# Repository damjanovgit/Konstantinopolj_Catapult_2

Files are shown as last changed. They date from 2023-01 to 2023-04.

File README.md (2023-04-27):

# Konstantinopolj_Catapult_2
Микроконтролерски системи/Рачунарска електроника, зимски семестар, ак. 2022/2023. година
<br />
<br />
<p align="center">


# Упутство за повезивање катапулта

## Напајање плочице
<p align="justify">Како је задано и пројектним задатком, напајање које се доводи на плочицу износи 12 V. Напајање се у овом случају доводи са протоборда (кориштењем мултиметра претходно је  увијек неопходно провјерити да ли напајање доиста одговара 12 V), а на слици су приказана и минимална повезивања. Краткоспојник жуте боје одговара 12 V, док је плавим означено уземљење, као што се да примијетити на слици. 
<br />
<br />
<p align="center">


## Повезивање плочице са програматором 
<p align="justify">За програмирање микроконтролера користи се програматор PICkit верзије 3. Наредна слика показује pinout који користи овај програматор, при чему стрелица ка доле означава пин MCLR, односно, како је приказано ознакама на слици слијева:
<br />
<br />
<p align="center">


<p align="justify">На слици здесна приказано је повезивање програматора са плочицом. Пет конектора на које треба повезати пинове програматора налази се унутар црвеног блока, те редослијед који је претходно поменут важи уколико вршимо повезивање као на слици.

## Повезивање корачних мотора са плочицом

<p align="justify">За рад са катапултом кориштено је шест корачних мотора. Од тог броја два корачна мотора користе се за кретање ласера, преостала четири су на самом катапулту,означени са О (окретање), N (натезање), К (кашика) те P (пуцање). Мотор са ознаком О омогућава окретање самог катапулта, а претходно поменути мотори са ознакама N, K и  P приказани су  на слици испод. 
<br />
<br />


Слиједи и повезивање корачних мотора са плочицом. На слици је приказан распоред повезивања, гдје се неозначени корачни мотори односе на ласере. 
<br />
<br />
<p align="center">


## Повезивање са рачунаром

<p align="justify">За везу са рачунаром  користи се USB-UART модул. Са претходно инсталираном верзијом одговарајућег драјвера за FT232RL неопходно је повезати рачунар и модул који се налази на плочици. 

<br />
<br />
<p align="center">


## Програмирање и управљање катапултом
<p align="justify">Преостаје  упалити напајање, а затим на плочици омогућити програмирање микроконтролера. Наредна слика приказује које краткоспојнике треба повезати приликом програмирања (смеђи и зелени), а затим и након што се микроконтролер успјешно испрограмира (црни и зелени). 
<br />
<br />
<p align="center">


<p align="justify">Пројекат у MikroC-у (фолдер Software/PIC24) компајлирати, а затим изгенерисан .hex унијети у MPLAB IDE софтвер за програмирање. Ући у апликацију (софтвер Processing) и учитати пројекат (фолдер Software/Processing), да би  се затим управљало катапултом, са контролним командама наведеним у табели испод.
<br />
<br />

|  Команда | Функционалност 
|---|---
|  А или а | помјерање првог ласера улијево  
|  D или d | помјерање првог ласера удесно
|  J или j | помјерање другог ласера улијево 
|  L или l | помјерање другог ласера удесно
|  C или c | калибрација
|  S или s | синхронизација ласера са апликациjом
|  space | гађање мете

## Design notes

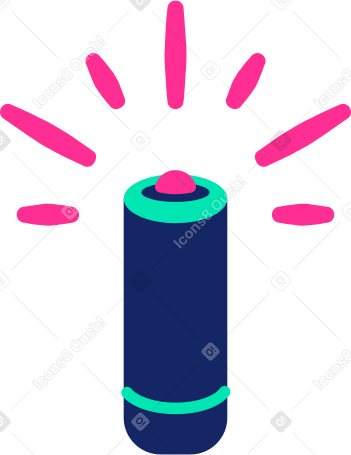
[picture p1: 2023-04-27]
Software/Processing/laser.png

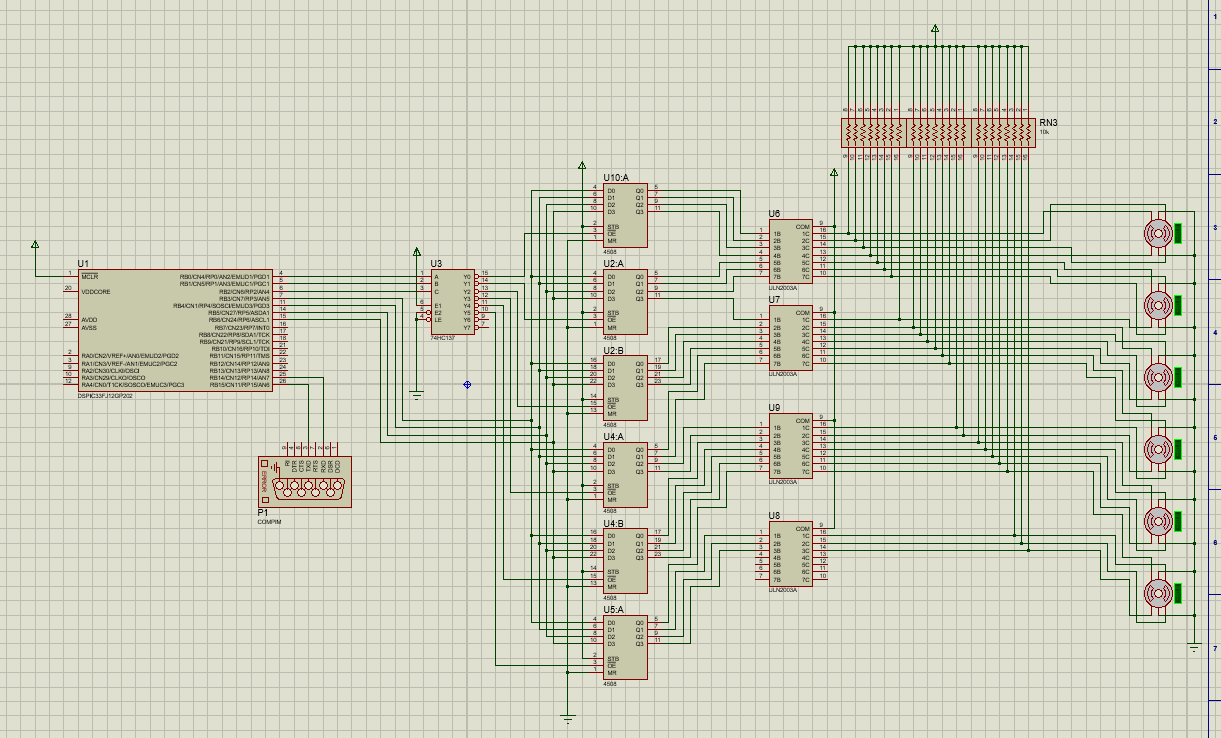
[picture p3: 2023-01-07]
Proteus simulacija/Sema.png

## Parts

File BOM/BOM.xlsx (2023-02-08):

Date: | 31-1-2023
Tool: | Eeschema (6.0.2)
Component Count: | 95
Individual Components:
Item | Qty | Reference(s) | Value | Footprint
 |  | C0 | 0.1uF | footprints:08055A220JAT2A
 |  | C1 | 0.1uF | footprints:08055A220JAT2A
 |  | C2 | 100uF | footprints:08055A220JAT2A
 |  | C3 | 22pF | footprints:08055A220JAT2A
 |  | C4 | 22pF | footprints:08055A220JAT2A
 |  | C5 | 0.1uF | footprints:08055A220JAT2A
 |  | C6 | 0.1uF | footprints:08055A220JAT2A
 |  | C7 | 100uF | footprints:08055A220JAT2A
 |  | C8 | 0.1uF | footprints:08055A220JAT2A
 |  | C9 | 0.1uF | footprints:08055A220JAT2A
 |  | C10 | 0.1uF | footprints:08055A220JAT2A
 |  | C11 | 0.1uF | footprints:08055A220JAT2A
 |  | C12 | 10uF | footprints:08055A220JAT2A
 |  | C13 | 0.1uF | footprints:08055A220JAT2A
 |  | C14 | 0.1uF | footprints:08055A220JAT2A
 |  | C15 | 0.1uF | footprints:08055A220JAT2A
 |  | C16 | 0.1uF | footprints:08055A220JAT2A
 |  | C17 | 0.1uF | footprints:08055A220JAT2A
 |  | C18 | 0.1uF | footprints:08055A220JAT2A
 |  | C19 | 0.1uF | footprints:08055A220JAT2A
 |  | C20 | 0.1uF | footprints:08055A220JAT2A
 |  | C21 | 0.1uF | footprints:08055A220JAT2A
 |  | C22 | 0.1uF | footprints:08055A220JAT2A
 |  | H1 | MountingHole | MountingHole:MountingHole_3.5mm | ~
 |  | H2 | MountingHole | MountingHole:MountingHole_3.5mm | ~
 |  | H3 | MountingHole | MountingHole:MountingHole_3.5mm | ~
 |  | H4 | MountingHole | MountingHole:MountingHole_3.5mm | ~
 |  | J1 | Conn_01x05_Male | Connector_PinHeader_1.00mm:PinHeader_1x05_P1.00mm_Vertical | ~
 |  | J2 | Conn_01x01_Male | Connector_PinHeader_1.00mm:PinHeader_1x01_P1.00mm_Vertical | ~
 |  | J3 | Conn_01x03_Male | Connector_PinHeader_1.00mm:PinHeader_1x03_P1.00mm_Vertical | ~
 |  | J4 | Conn_01x05_Male | Connector_PinHeader_1.00mm:PinHeader_1x05_P1.00mm_Vertical | ~
 |  | J5 | Conn_01x03_Male | Connector_PinHeader_1.00mm:PinHeader_1x03_P1.00mm_Vertical | ~
 |  | J6 | USB_B | Connector_USB:USB_B_TE_5787834_Vertical | ~
 |  | J7 | Conn_01x05_Male | Connector_PinHeader_1.00mm:PinHeader_1x05_P1.00mm_Vertical | ~
 |  | J8 | Conn_01x05_Male | Connector_PinHeader_1.00mm:PinHeader_1x05_P1.00mm_Vertical | ~
 |  | J9 | Conn_01x05_Male | Connector_PinHeader_1.00mm:PinHeader_1x05_P1.00mm_Vertical | ~
 |  | J10 | Conn_01x05_Male | Connector_PinHeader_1.00mm:PinHeader_1x05_P1.00mm_Vertical | ~
 |  | J11 | Conn_01x05_Male | Connector_PinHeader_1.00mm:PinHeader_1x05_P1.00mm_Vertical | ~
 |  | J12 | Conn_01x05_Male | Connector_PinHeader_1.00mm:PinHeader_1x05_P1.00mm_Vertical | ~
 |  | J13 | Conn_01x01_Male | Connector_PinHeader_1.00mm:PinHeader_1x01_P1.00mm_Vertical | ~
 |  | J14 | Conn_01x01_Male | Connector_PinHeader_1.00mm:PinHeader_1x01_P1.00mm_Vertical | ~
 |  | J15 | Conn_01x01_Male | Connector_PinHeader_1.00mm:PinHeader_1x01_P1.00mm_Vertical | ~
 |  | J16 | Conn_01x01_Male | Connector_PinHeader_1.00mm:PinHeader_1x01_P1.00mm_Vertical | ~
 |  | R1 | 10k | HCJ0805ZT0R00j:HCJ0805ZT0R00
 |  | R2 | 10k | HCJ0805ZT0R00j:HCJ0805ZT0R00
 |  | R3 | 270 | HCJ0805ZT0R00j:HCJ0805ZT0R00
 |  | R4 | 820 | HCJ0805ZT0R00j:HCJ0805ZT0R00
 |  | R5 | 300 | HCJ0805ZT0R00j:HCJ0805ZT0R00
 |  | R6 | 7.5k | HCJ0805ZT0R00j:HCJ0805ZT0R00
 |  | R7 | 10k | HCJ0805ZT0R00j:HCJ0805ZT0R00
 |  | R8 | 10k | HCJ0805ZT0R00j:HCJ0805ZT0R00
 |  | R9 | 10k | HCJ0805ZT0R00j:HCJ0805ZT0R00
 |  | R10 | 10k | HCJ0805ZT0R00j:HCJ0805ZT0R00
 |  | R11 | 10k | HCJ0805ZT0R00j:HCJ0805ZT0R00
 |  | R12 | 10k | HCJ0805ZT0R00j:HCJ0805ZT0R00
 |  | R13 | 10k | HCJ0805ZT0R00j:HCJ0805ZT0R00
 |  | R14 | 10k | HCJ0805ZT0R00j:HCJ0805ZT0R00
 |  | TP1 | TestPoint | Connector_PinHeader_1.00mm:PinHeader_1x01_P1.00mm_Vertical | ~
 |  | TP1.1 | TestPoint_Small | Connector_PinHeader_1.00mm:PinHeader_1x01_P1.00mm_Vertical | ~
 |  | TP1.2 | TestPoint_Small | Connector_PinHeader_1.00mm:PinHeader_1x01_P1.00mm_Vertical | ~
 |  | TP2 | TestPoint | Connector_PinHeader_1.00mm:PinHeader_1x01_P1.00mm_Vertical | ~
 |  | TP2.1 | TestPoint_Small | Connector_PinHeader_1.00mm:PinHeader_1x01_P1.00mm_Vertical | ~
 |  | TP2.2 | TestPoint_Small | Connector_PinHeader_1.00mm:PinHeader_1x01_P1.00mm_Vertical | ~
 |  | TP3 | TestPoint | Connector_PinHeader_1.00mm:PinHeader_1x01_P1.00mm_Vertical | ~
 |  | TP3.1 | TestPoint_Small | Connector_PinHeader_1.00mm:PinHeader_1x01_P1.00mm_Vertical | ~
 |  | TP3.2 | TestPoint_Small | Connector_PinHeader_1.00mm:PinHeader_1x01_P1.00mm_Vertical | ~
 |  | TP4 | TestPoint | Connector_PinHeader_1.00mm:PinHeader_1x01_P1.00mm_Vertical | ~
 |  | TP4.1 | TestPoint_Small | Connector_PinHeader_1.00mm:PinHeader_1x01_P1.00mm_Vertical | ~
 |  | TP4.2 | TestPoint_Small | Connector_PinHeader_1.00mm:PinHeader_1x01_P1.00mm_Vertical | ~
 |  | TP5 | TestPoint | Connector_PinHeader_1.00mm:PinHeader_1x01_P1.00mm_Vertical | ~
 |  | TP5.1 | TestPoint_Small | Connector_PinHeader_1.00mm:PinHeader_1x01_P1.00mm_Vertical | ~
 |  | TP5.2 | TestPoint_Small | Connector_PinHeader_1.00mm:PinHeader_1x01_P1.00mm_Vertical | ~
 |  | TP6 | TestPoint | Connector_PinHeader_1.00mm:PinHeader_1x01_P1.00mm_Vertical | ~
 |  | TP7 | TestPoint | Connector_PinHeader_1.00mm:PinHeader_1x01_P1.00mm_Vertical | ~
 |  | TP8 | TestPoint | Connector_PinHeader_1.00mm:PinHeader_1x01_P1.00mm_Vertical | ~
 |  | TP9 | TestPoint | Connector_PinHeader_1.00mm:PinHeader_1x01_P1.00mm_Vertical | ~
 |  | TP10 | TestPoint | Connector_PinHeader_1.00mm:PinHeader_1x01_P1.00mm_Vertical | ~
 |  | TP11 | TestPoint | Connector_PinHeader_1.00mm:PinHeader_1x01_P1.00mm_Vertical | ~
 |  | U1 | LM317AT/NOPB | LM317AT:LM317AT
 |  | U2 | LM317AT/NOPB | LM317AT:LM317AT
 |  | U3 | PIC24FJ64GA702-I/SO | PIC24FJ64GA702-ISO:PIC24FJ64GA702-I&slash_SO
 |  | U4 | ABLS-8.000MHZ-B2-T | ABLS-8:ABLS-8.000MHZ-B2-T
 |  | U5 | FT232RL | Package_SO:SSOP-28_5.3x10.2mm_P0.65mm
 |  | U6 | CD74HC4514M96 | CD74HC4514M96j:CD74HC4514M96
 |  | U7 | PTMUX1308QDYYRQ1 | PTMUX1308QDYYRQ1j:PTMUX1308QDYYRQ1
 |  | U8 | 74LVT573MTC | 74LVT573MTCj:74LVT573MTC
 |  | U9 | 74LVT573MTC | 74LVT573MTCj:74LVT573MTC
 |  | U10 | 74LVT573MTC | 74LVT573MTCj:74LVT573MTC
 |  | U11 | 74LVT573MTC | 74LVT573MTCj:74LVT573MTC
 |  | U12 | 74LVT573MTC | 74LVT573MTCj:74LVT573MTC
 |  | U13 | 74LVT573MTC | 74LVT573MTCj:74LVT573MTC
 |  | U14 | ULN2003AIDR | ULN2003AIDRj:ULN2003AIDR
 |  | U15 | ULN2003AIDR | ULN2003AIDRj:ULN2003AIDR
 |  | U16 | ULN2003AIDR | ULN2003AIDRj:ULN2003AIDR
 |  | U17 | ULN2003AIDR | ULN2003AIDRj:ULN2003AIDR
Collated Components:
Item | Qty | Reference(s) | Value | Footprint | Mouser Part No. | Link to Mouser
1 | 1 | C0 | 0.1uF | footprints:08055A220JAT2A | 80-C0805C104K5RACLR | https://eu.mouser.com/ProductDetail/KEMET/C0805C104K5RAC7411
2 | 17 | C1, C5, C6, C8, C9, C10, C11, C13, C14, C15, C16, C17, C18, C19, C20, C21, C22 | 0.1uF | footprints:08055A220JAT2A | 80-C0805C104K5RACLR
3 | 1 | C2 | 100uF | footprints:08055A220JAT2A | 581-CM21X5R107M06AT | https://eu.mouser.com/ProductDetail/KYOCERA-AVX/CM21X5R107M06AT
4 | 2 | C3, C4 | 22pF | footprints:08055A220JAT2A | 581-08055A220J | https://eu.mouser.com/ProductDetail/KYOCERA-AVX/08055A220JAT2A?qs=owscpGBW86WTFbKrxpDmHA%3D%3D
5 | 1 | C7 | 100uF | footprints:08055A220JAT2A | 581-CM21X5R107M06AT
6 | 1 | C12 | 10uF | footprints:08055A220JAT2A | 581-0805YC106KAT2A | https://eu.mouser.com/ProductDetail/KYOCERA-AVX/0805YC106KAT2A
7 | 4 | H1, H2, H3, H4 | MountingHole | MountingHole:MountingHole_3.5mm
8 | 8 | J1, J4, J7, J8, J9, J10, J11, J12 | Conn_01x05_Male | Connector_PinHeader_1.00mm:PinHeader_1x05_P1.00mm_Vertical
9 | 5 | J2, J13, J14, J15, J16 | Conn_01x01_Male | Connector_PinHeader_1.00mm:PinHeader_1x01_P1.00mm_Vertical
10 | 2 | J3, J5 | Conn_01x03_Male | Connector_PinHeader_1.00mm:PinHeader_1x03_P1.00mm_Vertical
11 | 1 | J6 | USB_B | Connector_USB:USB_B_TE_5787834_Vertical | 806-KUSBEXSMTBS1NBTR | https://eu.mouser.com/ProductDetail/Kycon/KUSBEX-SMT-BS1N-BTR?qs=Dwx6NbQqjSszQKAJMTcyOA%3D%3D
12 | 10 | R1, R2, R7, R8, R9, R10, R11, R12, R13, R14 | 10k | HCJ0805ZT0R00j:HCJ0805ZT0R00 | 652-CMP0805AFX-1002L | https://eu.mouser.com/ProductDetail/Bourns/CMP0805AFX-1002ELF
13 | 1 | R3 | 270 | HCJ0805ZT0R00j:HCJ0805ZT0R00 | 652-CR0805JW-271ELF | https://eu.mouser.com/ProductDetail/Bourns/CR0805-JW-271ELF
14 | 1 | R4 | 820 | HCJ0805ZT0R00j:HCJ0805ZT0R00 | 652-CR0805-JW-821EPF | https://eu.mouser.com/ProductDetail/Bourns/CR0805-JW-821EPF
15 | 1 | R5 | 300 | HCJ0805ZT0R00j:HCJ0805ZT0R00 | 652-CR0805JW-301ELF | https://eu.mouser.com/ProductDetail/Bourns/CR0805-JW-301ELF
16 | 1 | R6 | 7.5k | HCJ0805ZT0R00j:HCJ0805ZT0R00 | 652-CR0805FX-7501ELF | https://eu.mouser.com/ProductDetail/Bourns/CR0805-FX-7501ELF?qs=sGAEpiMZZMtlubZbdhIBICRqbmKbZF9w9OAhIRC8MF8%3D
17 | 11 | TP1, TP2, TP3, TP4, TP5, TP6, TP7, TP8, TP9, TP10, TP11 | TestPoint | Connector_PinHeader_1.00mm:PinHeader_1x01_P1.00mm_Vertical
18 | 10 | TP1.1, TP1.2, TP2.1, TP2.2, TP3.1, TP3.2, TP4.1, TP4.2, TP5.1, TP5.2 | TestPoint_Small | Connector_PinHeader_1.00mm:PinHeader_1x01_P1.00mm_Vertical
19 | 2 | U1, U2 | LM317AT/NOPB | LM317AT:LM317AT | 863-LM317MADTRKG | https://eu.mouser.com/ProductDetail/onsemi/LM317MADTRKG?qs=2OtswVQKCOFlhMcZfF6npw%3D%3D
20 | 1 | U3 | PIC24FJ64GA702-I/SO | PIC24FJ64GA702-ISO:PIC24FJ64GA702-I&slash_SO | 579-24FJ64GA702ISO | https://eu.mouser.com/ProductDetail/Microchip-Technology-Atmel/PIC24FJ64GA702-I-SO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
21 | 1 | U4 | ABLS-8.000MHZ-B2-T | ABLS-8:ABLS-8.000MHZ-B2-T | 815-ABLS-8-B2 | https://eu.mouser.com/ProductDetail/ABRACON/ABLS-8.000MHZ-B2-T?qs=H8AWquzS%2FlOPBpG0T30dWA%3D%3D
22 | 1 | U5 | FT232RL | Package_SO:SSOP-28_5.3x10.2mm_P0.65mm | 895-FT232RL | https://eu.mouser.com/ProductDetail/FTDI/FT232RL-REEL?qs=D1%2FPMqvA103RC6OU6bKtoA%3D%3D
23 | 1 | U6 | CD74HC4514M96 | CD74HC4514M96j:CD74HC4514M96 | 595-CD74HC4514M96 | https://eu.mouser.com/ProductDetail/Texas-Instruments/CD74HC4514M96?qs=xFfolx0DHx3s6ILXGQ%2FrLQ%3D%3D
24 | 1 | U7 | PTMUX1308QDYYRQ1 | PTMUX1308QDYYRQ1j:PTMUX1308QDYYRQ1 | 595-TMUX1308QDYYRQ1 | https://eu.mouser.com/ProductDetail/Texas-Instruments/TMUX1308QDYYRQ1?qs=xZ%2FP%252Ba9zWqaqz9D2kpWQ%2FA%3D%3D
25 | 6 | U8, U9, U10, U11, U12, U13 | 74LVT573MTC | 74LVT573MTCj:74LVT573MTC | 512-74LVT573MTCX | https://eu.mouser.com/ProductDetail/onsemi-Fairchild/74LVT573MTCX?qs=nW0pe8qlIZhn3pN6dK8f5Q%3D%3D
26 | 4 | U14, U15, U16, U17 | ULN2003AIDR | ULN2003AIDRj:ULN2003AIDR | 595-ULN2003AIDR | https://eu.mouser.com/ProductDetail/Texas-Instruments/ULN2003AIDR?qs=pbofycSusePLfAeFJ8tqkg%3D%3D

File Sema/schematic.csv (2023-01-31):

Source: | D:\IV\Racunarska elektronika\projektni_zadatak\project_git\Konstantinopolj_Catapult_2\Sema\schematic.kicad_sch
Date: | 1/31/2023 10:14:45 AM
Tool: | Eeschema (6.0.2)
Generator: | C:\Program Files\KiCad\6.0\bin\scripting\plugins/bom_csv_grouped_by_value.py
Component Count: | 95
Individual Components:
Item | Qty | Reference(s) | Value | LibPart | Footprint | Datasheet
 |  | 0.1uF1 | 08055A220JAT2A | 2022-12-14_18-04-28:08055A220JAT2A | footprints:08055A220JAT2A
 |  | C1 | 0.1uF | 2022-12-14_18-04-28:08055A220JAT2A | footprints:08055A220JAT2A
 |  | C2 | 100uF | 2022-12-14_18-04-28:08055A220JAT2A | footprints:08055A220JAT2A
 |  | C3 | 22pF | 2022-12-14_18-04-28:08055A220JAT2A | footprints:08055A220JAT2A
 |  | C4 | 22pF | 2022-12-14_18-04-28:08055A220JAT2A | footprints:08055A220JAT2A
 |  | C5 | 0.1uF | 2022-12-14_18-04-28:08055A220JAT2A | footprints:08055A220JAT2A
 |  | C6 | 0.1uF | 2022-12-14_18-04-28:08055A220JAT2A | footprints:08055A220JAT2A
 |  | C7 | 100uf | 2022-12-14_18-04-28:08055A220JAT2A | footprints:08055A220JAT2A
 |  | C8 | 0.1uF | 2022-12-14_18-04-28:08055A220JAT2A | footprints:08055A220JAT2A
 |  | C9 | 0.1uF | 2022-12-14_18-04-28:08055A220JAT2A | footprints:08055A220JAT2A
 |  | C10 | 0.1uF | 2022-12-14_18-04-28:08055A220JAT2A | footprints:08055A220JAT2A
 |  | C11 | 0.1uF | 2022-12-14_18-04-28:08055A220JAT2A | footprints:08055A220JAT2A
 |  | C12 | 10uF | 2022-12-14_18-04-28:08055A220JAT2A | footprints:08055A220JAT2A
 |  | C13 | 0.1uF | 2022-12-14_18-04-28:08055A220JAT2A | footprints:08055A220JAT2A
 |  | C14 | 0.1uF | 2022-12-14_18-04-28:08055A220JAT2A | footprints:08055A220JAT2A
 |  | C15 | 0.1uF | 2022-12-14_18-04-28:08055A220JAT2A | footprints:08055A220JAT2A
 |  | C16 | 0.1uF | 2022-12-14_18-04-28:08055A220JAT2A | footprints:08055A220JAT2A
 |  | C17 | 0.1uF | 2022-12-14_18-04-28:08055A220JAT2A | footprints:08055A220JAT2A
 |  | C18 | 0.1uF | 2022-12-14_18-04-28:08055A220JAT2A | footprints:08055A220JAT2A
 |  | C19 | 0.1uF | 2022-12-14_18-04-28:08055A220JAT2A | footprints:08055A220JAT2A
 |  | C20 | 0.1uF | 2022-12-14_18-04-28:08055A220JAT2A | footprints:08055A220JAT2A
 |  | C21 | 0.1uF | 2022-12-14_18-04-28:08055A220JAT2A | footprints:08055A220JAT2A
 |  | C22 | 0.1uF | 2022-12-14_18-04-28:08055A220JAT2A | footprints:08055A220JAT2A
 |  | H1 | MountingHole | Mechanical:MountingHole | MountingHole:MountingHole_3.5mm | ~
 |  | H2 | MountingHole | Mechanical:MountingHole | MountingHole:MountingHole_3.5mm | ~
 |  | H3 | MountingHole | Mechanical:MountingHole | MountingHole:MountingHole_3.5mm | ~
 |  | H4 | MountingHole | Mechanical:MountingHole | MountingHole:MountingHole_3.5mm | ~
 |  | J1 | Conn_01x05_Male | Connector:Conn_01x05_Male | Connector_PinHeader_1.00mm:PinHeader_1x05_P1.00mm_Vertical | ~
 |  | J2 | Conn_01x01_Male | Connector:Conn_01x01_Male | Connector_PinHeader_1.00mm:PinHeader_1x01_P1.00mm_Vertical | ~
 |  | J3 | Conn_01x03_Male | Connector:Conn_01x03_Male | Connector_PinHeader_1.00mm:PinHeader_1x03_P1.00mm_Vertical | ~
 |  | J4 | Conn_01x05_Male | Connector:Conn_01x05_Male | Connector_PinHeader_1.00mm:PinHeader_1x05_P1.00mm_Vertical | ~
 |  | J5 | Conn_01x03_Male | Connector:Conn_01x03_Male | Connector_PinHeader_1.00mm:PinHeader_1x03_P1.00mm_Vertical | ~
 |  | J6 | USB_B | Connector:USB_B | Connector_USB:USB_B_TE_5787834_Vertical | ~
 |  | J7 | Conn_01x05_Male | Connector:Conn_01x05_Male | Connector_PinHeader_1.00mm:PinHeader_1x05_P1.00mm_Vertical | ~
 |  | J8 | Conn_01x05_Male | Connector:Conn_01x05_Male | Connector_PinHeader_1.00mm:PinHeader_1x05_P1.00mm_Vertical | ~
 |  | J9 | Conn_01x05_Male | Connector:Conn_01x05_Male | Connector_PinHeader_1.00mm:PinHeader_1x05_P1.00mm_Vertical | ~
 |  | J10 | Conn_01x05_Male | Connector:Conn_01x05_Male | Connector_PinHeader_1.00mm:PinHeader_1x05_P1.00mm_Vertical | ~
 |  | J11 | Conn_01x05_Male | Connector:Conn_01x05_Male | Connector_PinHeader_1.00mm:PinHeader_1x05_P1.00mm_Vertical | ~
 |  | J12 | Conn_01x05_Male | Connector:Conn_01x05_Male | Connector_PinHeader_1.00mm:PinHeader_1x05_P1.00mm_Vertical | ~
 |  | J13 | Conn_01x01_Male | Connector:Conn_01x01_Male | Connector_PinHeader_1.00mm:PinHeader_1x01_P1.00mm_Vertical | ~
 |  | J14 | Conn_01x01_Male | Connector:Conn_01x01_Male | Connector_PinHeader_1.00mm:PinHeader_1x01_P1.00mm_Vertical | ~
 |  | J15 | Conn_01x01_Male | Connector:Conn_01x01_Male | Connector_PinHeader_1.00mm:PinHeader_1x01_P1.00mm_Vertical | ~
 |  | J16 | Conn_01x01_Male | Connector:Conn_01x01_Male | Connector_PinHeader_1.00mm:PinHeader_1x01_P1.00mm_Vertical | ~
 |  | R1 | 10k | HCJ0805ZT0R00:HCJ0805ZT0R00 | HCJ0805ZT0R00j:HCJ0805ZT0R00
 |  | R2 | 10k | HCJ0805ZT0R00:HCJ0805ZT0R00 | HCJ0805ZT0R00j:HCJ0805ZT0R00
 |  | R3 | 270 | HCJ0805ZT0R00:HCJ0805ZT0R00 | HCJ0805ZT0R00j:HCJ0805ZT0R00
 |  | R4 | 820 | HCJ0805ZT0R00:HCJ0805ZT0R00 | HCJ0805ZT0R00j:HCJ0805ZT0R00
 |  | R5 | 300 | HCJ0805ZT0R00:HCJ0805ZT0R00 | HCJ0805ZT0R00j:HCJ0805ZT0R00
 |  | R6 | 7.5k | HCJ0805ZT0R00:HCJ0805ZT0R00 | HCJ0805ZT0R00j:HCJ0805ZT0R00
 |  | R7 | 10k | HCJ0805ZT0R00:HCJ0805ZT0R00 | HCJ0805ZT0R00j:HCJ0805ZT0R00
 |  | R8 | 10k | HCJ0805ZT0R00:HCJ0805ZT0R00 | HCJ0805ZT0R00j:HCJ0805ZT0R00
 |  | R9 | 10k | HCJ0805ZT0R00:HCJ0805ZT0R00 | HCJ0805ZT0R00j:HCJ0805ZT0R00
 |  | R10 | 10k | HCJ0805ZT0R00:HCJ0805ZT0R00 | HCJ0805ZT0R00j:HCJ0805ZT0R00
 |  | R11 | 10k | HCJ0805ZT0R00:HCJ0805ZT0R00 | HCJ0805ZT0R00j:HCJ0805ZT0R00
 |  | R12 | 10k | HCJ0805ZT0R00:HCJ0805ZT0R00 | HCJ0805ZT0R00j:HCJ0805ZT0R00
 |  | R13 | 10k | HCJ0805ZT0R00:HCJ0805ZT0R00 | HCJ0805ZT0R00j:HCJ0805ZT0R00
 |  | R14 | 10k | HCJ0805ZT0R00:HCJ0805ZT0R00 | HCJ0805ZT0R00j:HCJ0805ZT0R00
 |  | TP1 | TestPoint | Connector:TestPoint | Connector_PinHeader_1.00mm:PinHeader_1x01_P1.00mm_Vertical | ~
 |  | TP1.1 | TestPoint_Small | Connector:TestPoint_Small | Connector_PinHeader_1.00mm:PinHeader_1x01_P1.00mm_Vertical | ~
 |  | TP1.2 | TestPoint_Small | Connector:TestPoint_Small | Connector_PinHeader_1.00mm:PinHeader_1x01_P1.00mm_Vertical | ~
 |  | TP2 | TestPoint | Connector:TestPoint | Connector_PinHeader_1.00mm:PinHeader_1x01_P1.00mm_Vertical | ~
 |  | TP2.1 | TestPoint_Small | Connector:TestPoint_Small | Connector_PinHeader_1.00mm:PinHeader_1x01_P1.00mm_Vertical | ~
 |  | TP2.2 | TestPoint_Small | Connector:TestPoint_Small | Connector_PinHeader_1.00mm:PinHeader_1x01_P1.00mm_Vertical | ~
 |  | TP3 | TestPoint | Connector:TestPoint | Connector_PinHeader_1.00mm:PinHeader_1x01_P1.00mm_Vertical | ~
 |  | TP3.1 | TestPoint_Small | Connector:TestPoint_Small | Connector_PinHeader_1.00mm:PinHeader_1x01_P1.00mm_Vertical | ~
 |  | TP3.2 | TestPoint_Small | Connector:TestPoint_Small | Connector_PinHeader_1.00mm:PinHeader_1x01_P1.00mm_Vertical | ~
 |  | TP4 | TestPoint | Connector:TestPoint | Connector_PinHeader_1.00mm:PinHeader_1x01_P1.00mm_Vertical | ~
 |  | TP4.1 | TestPoint_Small | Connector:TestPoint_Small | Connector_PinHeader_1.00mm:PinHeader_1x01_P1.00mm_Vertical | ~
 |  | TP4.2 | TestPoint_Small | Connector:TestPoint_Small | Connector_PinHeader_1.00mm:PinHeader_1x01_P1.00mm_Vertical | ~
 |  | TP5 | TestPoint | Connector:TestPoint | Connector_PinHeader_1.00mm:PinHeader_1x01_P1.00mm_Vertical | ~
 |  | TP5.1 | TestPoint_Small | Connector:TestPoint_Small | Connector_PinHeader_1.00mm:PinHeader_1x01_P1.00mm_Vertical | ~
 |  | TP5.2 | TestPoint_Small | Connector:TestPoint_Small | Connector_PinHeader_1.00mm:PinHeader_1x01_P1.00mm_Vertical | ~
 |  | TP6 | TestPoint | Connector:TestPoint | Connector_PinHeader_1.00mm:PinHeader_1x01_P1.00mm_Vertical | ~
 |  | TP7 | TestPoint | Connector:TestPoint | Connector_PinHeader_1.00mm:PinHeader_1x01_P1.00mm_Vertical | ~
 |  | TP8 | TestPoint | Connector:TestPoint | Connector_PinHeader_1.00mm:PinHeader_1x01_P1.00mm_Vertical | ~
 |  | TP9 | TestPoint | Connector:TestPoint | Connector_PinHeader_1.00mm:PinHeader_1x01_P1.00mm_Vertical | ~
 |  | TP10 | TestPoint | Connector:TestPoint | Connector_PinHeader_1.00mm:PinHeader_1x01_P1.00mm_Vertical | ~
 |  | TP11 | TestPoint | Connector:TestPoint | Connector_PinHeader_1.00mm:PinHeader_1x01_P1.00mm_Vertical | ~
 |  | U1 | LM317AT/NOPB | LM317AT&slash_NOPB:LM317AT{slash}NOPB | LM317AT:LM317AT
 |  | U2 | LM317AT/NOPB | LM317AT&slash_NOPB:LM317AT{slash}NOPB | LM317AT:LM317AT
 |  | U3 | PIC24FJ64GA702-I/SO | PIC24FJ64GA702-ISO:PIC24FJ64GA702-I{slash}SO | PIC24FJ64GA702-ISO:PIC24FJ64GA702-I&slash_SO
 |  | U4 | ABLS-8.000MHZ-B2-T | 2022-12-14_18-13-08:ABLS-8.000MHZ-B2-T | ABLS-8:ABLS-8.000MHZ-B2-T
 |  | U5 | FT232RL | Interface_USB:FT232RL | Package_SO:SSOP-28_5.3x10.2mm_P0.65mm | https://www.ftdichip.com/Support/Documents/DataSheets/ICs/DS_FT232R.pdf
 |  | U6 | CD74HC4514M96 | CD74HC4514M96:CD74HC4514M96 | CD74HC4514M96j:CD74HC4514M96
 |  | U7 | PTMUX1308QDYYRQ1 | 2023-01-18_13-22-56:PTMUX1308QDYYRQ1 | PTMUX1308QDYYRQ1j:PTMUX1308QDYYRQ1
 |  | U8 | 74LVT573MTC | 74LVT573MTC:74LVT573MTC | 74LVT573MTCj:74LVT573MTC
 |  | U9 | 74LVT573MTC | 74LVT573MTC:74LVT573MTC | 74LVT573MTCj:74LVT573MTC
 |  | U10 | 74LVT573MTC | 74LVT573MTC:74LVT573MTC | 74LVT573MTCj:74LVT573MTC
 |  | U11 | 74LVT573MTC | 74LVT573MTC:74LVT573MTC | 74LVT573MTCj:74LVT573MTC
 |  | U12 | 74LVT573MTC | 74LVT573MTC:74LVT573MTC | 74LVT573MTCj:74LVT573MTC
 |  | U13 | 74LVT573MTC | 74LVT573MTC:74LVT573MTC | 74LVT573MTCj:74LVT573MTC
 |  | U14 | ULN2003AIDR | ULN2003AIDR:ULN2003AIDR | ULN2003AIDRj:ULN2003AIDR
 |  | U15 | ULN2003AIDR | ULN2003AIDR:ULN2003AIDR | ULN2003AIDRj:ULN2003AIDR
 |  | U16 | ULN2003AIDR | ULN2003AIDR:ULN2003AIDR | ULN2003AIDRj:ULN2003AIDR
 |  | U17 | ULN2003AIDR | ULN2003AIDR:ULN2003AIDR | ULN2003AIDRj:ULN2003AIDR
Collated Components:
Item | Qty | Reference(s) | Value | LibPart | Footprint | Datasheet
1 | 1 | 0.1uF1 | 08055A220JAT2A | 2022-12-14_18-04-28:08055A220JAT2A | footprints:08055A220JAT2A
2 | 17 | C1, C5, C6, C8, C9, C10, C11, C13, C14, C15, C16, C17, C18, C19, C20, C21, C22 | 0.1uF | 2022-12-14_18-04-28:08055A220JAT2A | footprints:08055A220JAT2A
3 | 1 | C2 | 100uF | 2022-12-14_18-04-28:08055A220JAT2A | footprints:08055A220JAT2A
4 | 2 | C3, C4 | 22pF | 2022-12-14_18-04-28:08055A220JAT2A | footprints:08055A220JAT2A
5 | 1 | C7 | 100uf | 2022-12-14_18-04-28:08055A220JAT2A | footprints:08055A220JAT2A
6 | 1 | C12 | 10uF | 2022-12-14_18-04-28:08055A220JAT2A | footprints:08055A220JAT2A
7 | 4 | H1, H2, H3, H4 | MountingHole | Mechanical:MountingHole | MountingHole:MountingHole_3.5mm | ~
8 | 8 | J1, J4, J7, J8, J9, J10, J11, J12 | Conn_01x05_Male | Connector:Conn_01x05_Male | Connector_PinHeader_1.00mm:PinHeader_1x05_P1.00mm_Vertical | ~
9 | 5 | J2, J13, J14, J15, J16 | Conn_01x01_Male | Connector:Conn_01x01_Male | Connector_PinHeader_1.00mm:PinHeader_1x01_P1.00mm_Vertical | ~
10 | 2 | J3, J5 | Conn_01x03_Male | Connector:Conn_01x03_Male | Connector_PinHeader_1.00mm:PinHeader_1x03_P1.00mm_Vertical | ~
11 | 1 | J6 | USB_B | Connector:USB_B | Connector_USB:USB_B_TE_5787834_Vertical | ~
12 | 10 | R1, R2, R7, R8, R9, R10, R11, R12, R13, R14 | 10k | HCJ0805ZT0R00:HCJ0805ZT0R00 | HCJ0805ZT0R00j:HCJ0805ZT0R00
13 | 1 | R3 | 270 | HCJ0805ZT0R00:HCJ0805ZT0R00 | HCJ0805ZT0R00j:HCJ0805ZT0R00
14 | 1 | R4 | 820 | HCJ0805ZT0R00:HCJ0805ZT0R00 | HCJ0805ZT0R00j:HCJ0805ZT0R00
15 | 1 | R5 | 300 | HCJ0805ZT0R00:HCJ0805ZT0R00 | HCJ0805ZT0R00j:HCJ0805ZT0R00
16 | 1 | R6 | 7.5k | HCJ0805ZT0R00:HCJ0805ZT0R00 | HCJ0805ZT0R00j:HCJ0805ZT0R00
17 | 11 | TP1, TP2, TP3, TP4, TP5, TP6, TP7, TP8, TP9, TP10, TP11 | TestPoint | Connector:TestPoint | Connector_PinHeader_1.00mm:PinHeader_1x01_P1.00mm_Vertical | ~
18 | 10 | TP1.1, TP1.2, TP2.1, TP2.2, TP3.1, TP3.2, TP4.1, TP4.2, TP5.1, TP5.2 | TestPoint_Small | Connector:TestPoint_Small | Connector_PinHeader_1.00mm:PinHeader_1x01_P1.00mm_Vertical | ~
19 | 2 | U1, U2 | LM317AT/NOPB | LM317AT&slash_NOPB:LM317AT{slash}NOPB | LM317AT:LM317AT
20 | 1 | U3 | PIC24FJ64GA702-I/SO | PIC24FJ64GA702-ISO:PIC24FJ64GA702-I{slash}SO | PIC24FJ64GA702-ISO:PIC24FJ64GA702-I&slash_SO
21 | 1 | U4 | ABLS-8.000MHZ-B2-T | 2022-12-14_18-13-08:ABLS-8.000MHZ-B2-T | ABLS-8:ABLS-8.000MHZ-B2-T
22 | 1 | U5 | FT232RL | Interface_USB:FT232RL | Package_SO:SSOP-28_5.3x10.2mm_P0.65mm | https://www.ftdichip.com/Support/Documents/DataSheets/ICs/DS_FT232R.pdf
23 | 1 | U6 | CD74HC4514M96 | CD74HC4514M96:CD74HC4514M96 | CD74HC4514M96j:CD74HC4514M96
24 | 1 | U7 | PTMUX1308QDYYRQ1 | 2023-01-18_13-22-56:PTMUX1308QDYYRQ1 | PTMUX1308QDYYRQ1j:PTMUX1308QDYYRQ1
25 | 6 | U8, U9, U10, U11, U12, U13 | 74LVT573MTC | 74LVT573MTC:74LVT573MTC | 74LVT573MTCj:74LVT573MTC
26 | 4 | U14, U15, U16, U17 | ULN2003AIDR | ULN2003AIDR:ULN2003AIDR | ULN2003AIDRj:ULN2003AIDR

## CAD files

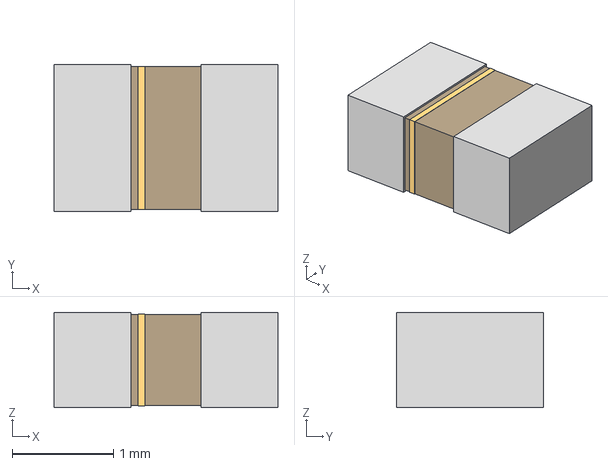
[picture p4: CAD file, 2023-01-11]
Sema/3D Models/08055A220JAT2A/CAP_0805J_AVX.step
2.21 x 1.45 x 0.94 mm

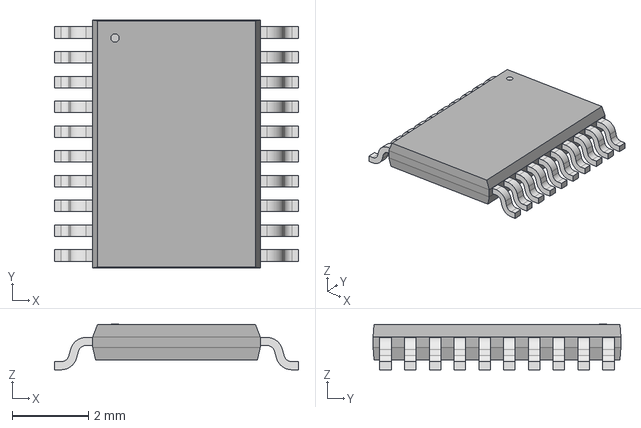
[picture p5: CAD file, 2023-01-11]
Sema/3D Models/74LVT573MTC3d/74LVT573MTC/TSSOP20_4P4X6P5_ONS.step
6.40 x 6.50 x 1.20 mm

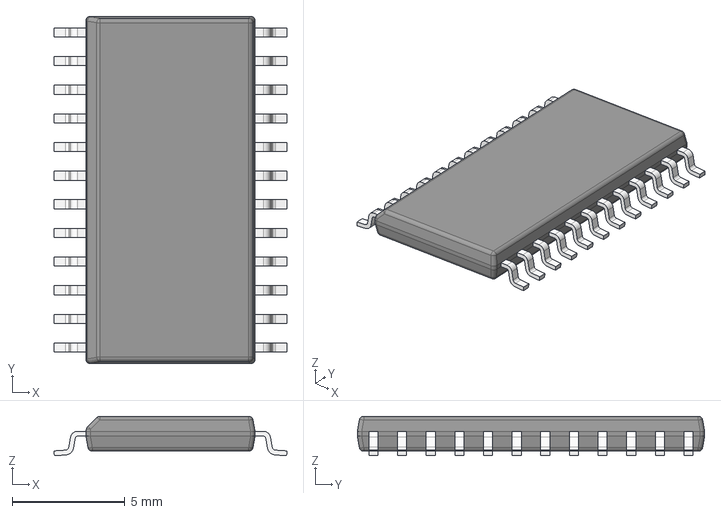
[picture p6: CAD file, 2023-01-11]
Sema/3D Models/CD74HC4514M96/DW0024B.stp
10.3 x 15.4 x 1.75 mm
BODY-SO
LEAD-SO x 24

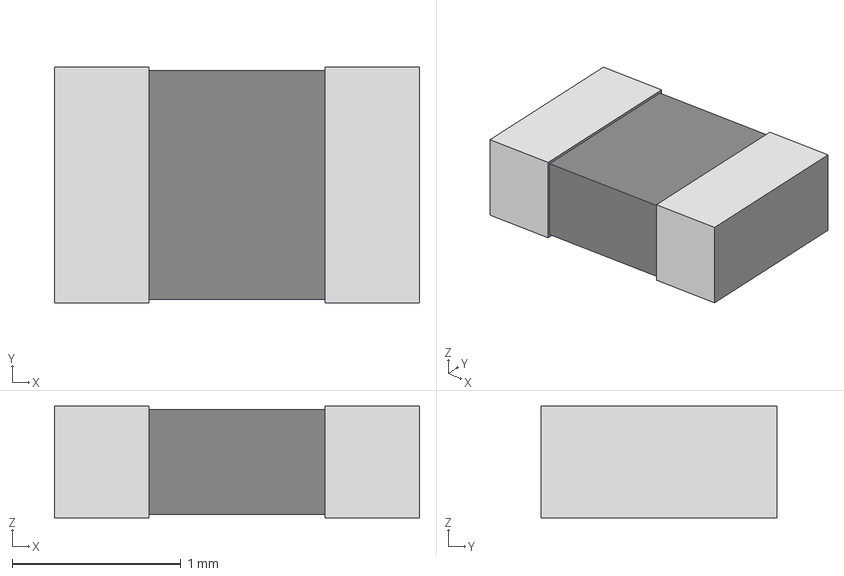
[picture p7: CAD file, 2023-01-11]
Sema/3D Models/HCJ0805ZT0R00/STA_HCJ0805_STP.step
2.16 x 1.40 x 0.66 mm

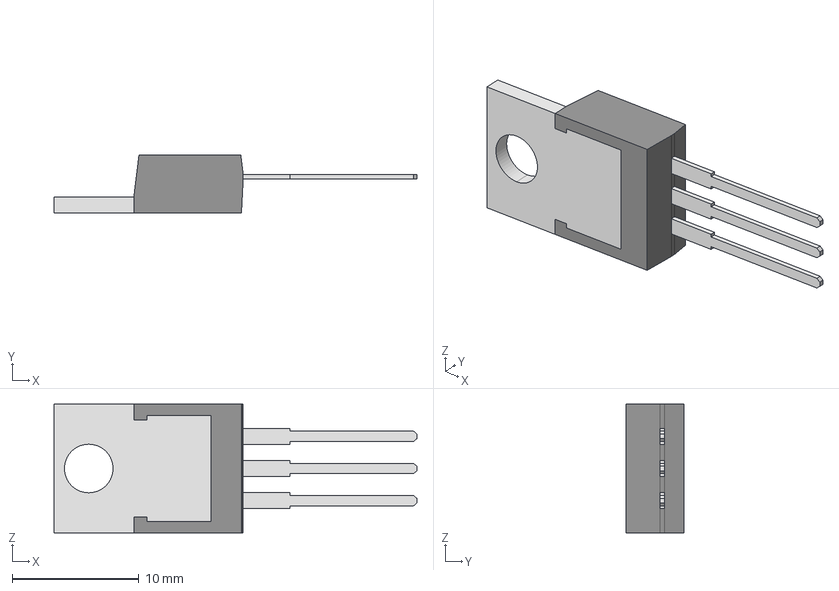
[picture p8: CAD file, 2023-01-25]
Sema/3D Models/LM317AT&slash_NOPB/NDE0003B.stp
28.7 x 4.57 x 10.2 mm
T03B_BODY
T03B_LEAD x 3
T03B_HS

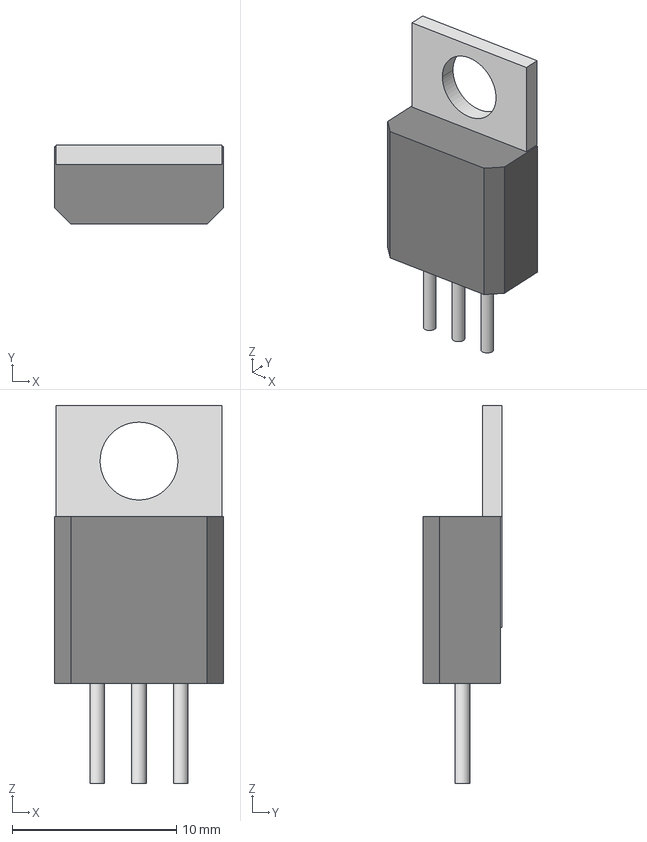
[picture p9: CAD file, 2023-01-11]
Sema/3D Models/LM317BTG/TO-220AB_ONS.step
10.3 x 4.83 x 23.0 mm

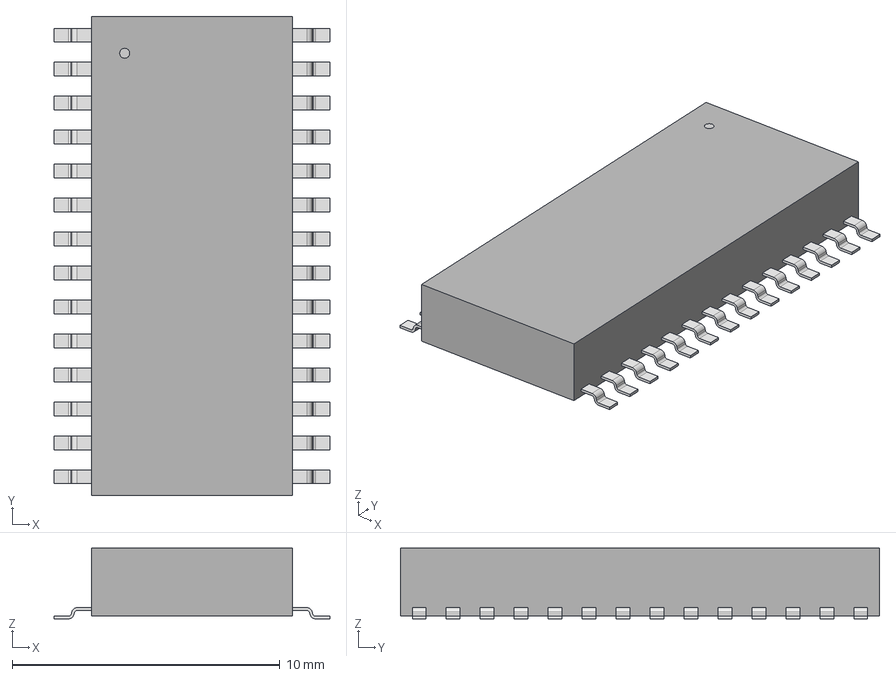
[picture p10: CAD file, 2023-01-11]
Sema/3D Models/PIC24FJ64GA702-ISO/SOIC28__SO28_MCH.step
10.3 x 17.9 x 2.64 mm

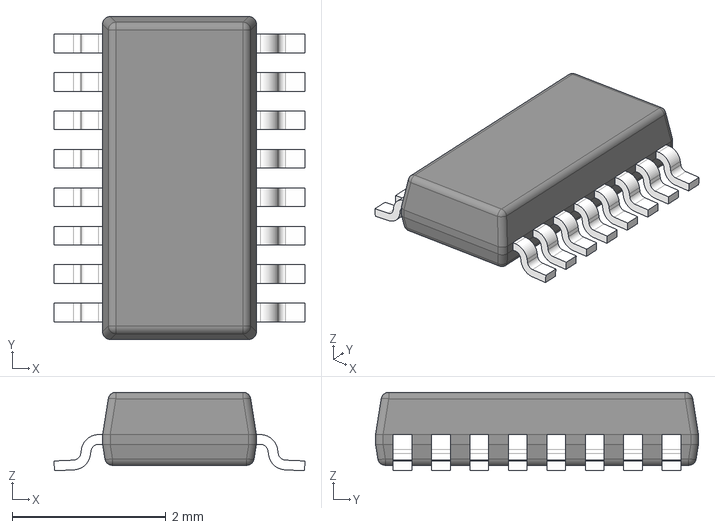
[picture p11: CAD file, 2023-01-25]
Sema/3D Models/PTMUX1308QDYYRQ1/DYY0016A.stp
3.26 x 4.20 x 1.02 mm
BODY-TSSOP
LEAD-TSSOP x 16

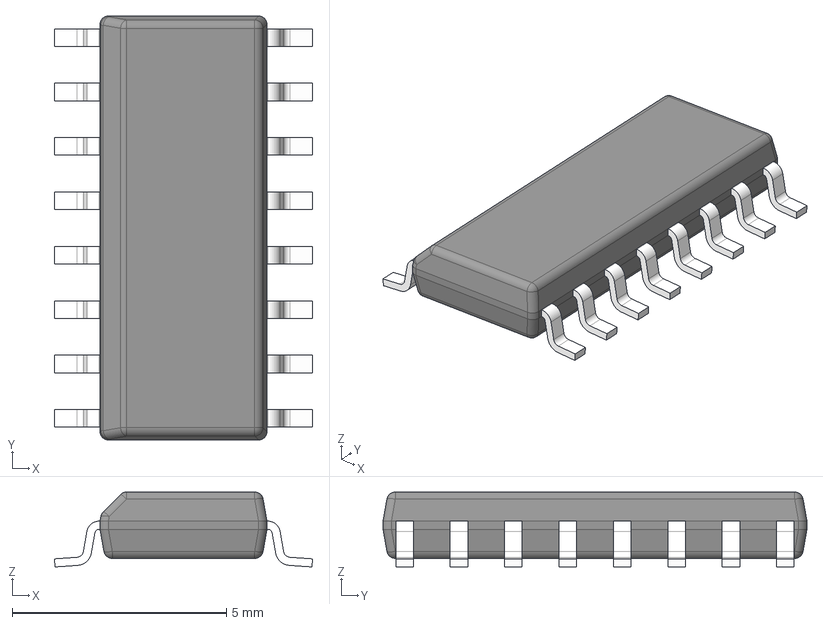
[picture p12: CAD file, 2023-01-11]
Sema/3D Models/SN74LS75DR/D0016A.stp
6.03 x 9.90 x 1.75 mm
BODY-SO
LEAD-SO x 16
PIN1-ID

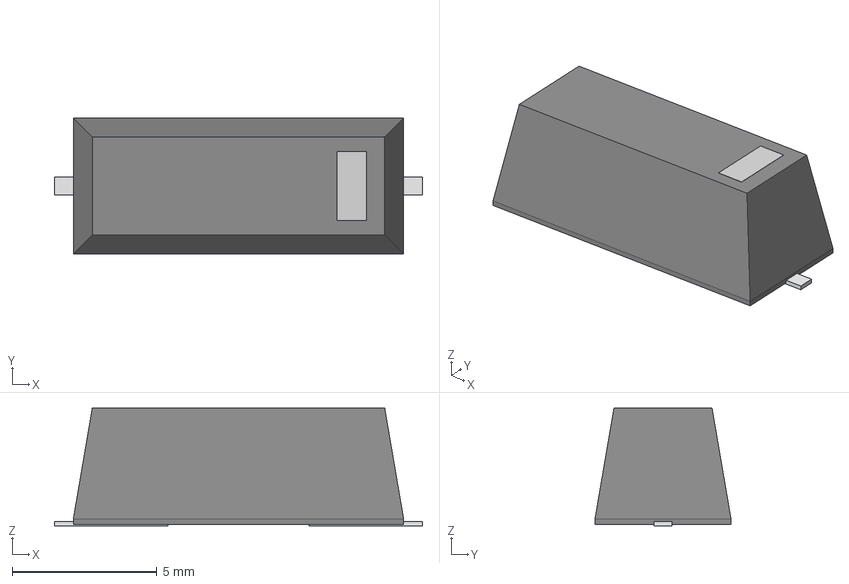
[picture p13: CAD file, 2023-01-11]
Sema/3D Models/STEP/ABLS-8_000MHZ-B2-T_ABR.step
12.7 x 4.70 x 4.07 mm

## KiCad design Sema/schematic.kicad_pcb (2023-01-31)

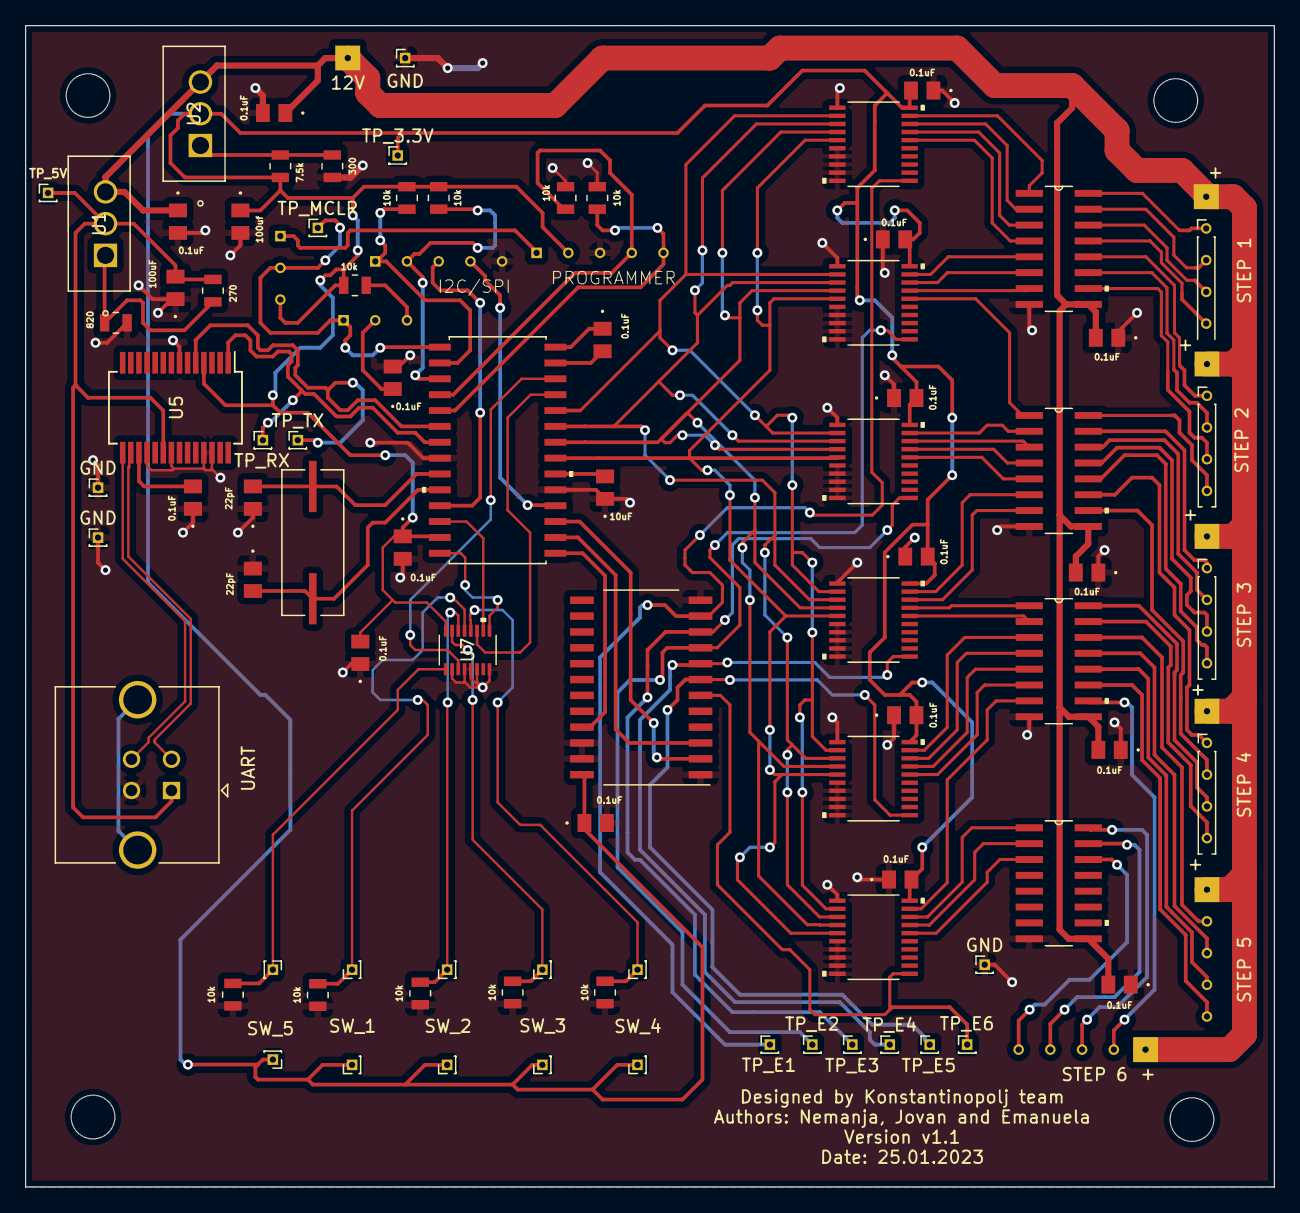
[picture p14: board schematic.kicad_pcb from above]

Board: 2 copper layers, 100.0 x 93.0 mm, 95 parts (0 on the bottom side), 96 nets.

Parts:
0.1uF1: 0.1uF; 08055A220JAT2A
12V: Conn_01x01_Male; PinHeader_1x01_P1.00mm_Vertical
C1, C5, C6, C8, C9, C10, C11, C13, C14, C15, C16, C17, C18, C19, C20, C21, C22: 0.1uF; 08055A220JAT2A
C2: 100uF; 08055A220JAT2A
C3, C4: 22pF; 08055A220JAT2A
C7: 100uf; 08055A220JAT2A
C12: 10uF; 08055A220JAT2A
GND: Conn_01x01_Male; PinHeader_1x01_P1.00mm_Vertical
GND#2, GND#3, GND#4: Conn_01x01_Male; PinHeader_1x01_P1.00mm_Vertical
H1, H2, H3, H4: MountingHole; MountingHole_3.5mm
J1, J4, J7, J8, J9, J10, J11, J12: Conn_01x05_Male; PinHeader_1x05_P1.00mm_Vertical
J3, J5: Conn_01x03_Male; PinHeader_1x03_P1.00mm_Vertical
R1, R2, R7, R8, R9, R10, R11, R12, R13, R14: 10k; HCJ0805ZT0R00
R3: 270; HCJ0805ZT0R00
R4: 820; HCJ0805ZT0R00
R5: 300; HCJ0805ZT0R00
R6: 7.5k; HCJ0805ZT0R00
SW_1, SW_2, SW_3, SW_4, SW_5: TestPoint_Small; PinHeader_1x01_P1.00mm_Vertical
TP1.1, TP2.1, TP3.1, TP4.1, TP5.1: TestPoint_Small; PinHeader_1x01_P1.00mm_Vertical
TP_3.3V, TP_5V: TestPoint; PinHeader_1x01_P1.00mm_Vertical
TP_E1, TP_E2, TP_E3, TP_E4, TP_E5, TP_E6: TestPoint; PinHeader_1x01_P1.00mm_Vertical
TP_MCLR: TestPoint; PinHeader_1x01_P1.00mm_Vertical
TP_RX: TestPoint; PinHeader_1x01_P1.00mm_Vertical
TP_TX: TestPoint; PinHeader_1x01_P1.00mm_Vertical
U1, U2: LM317AT/NOPB; LM317AT
U3: PIC24FJ64GA702-I/SO; PIC24FJ64GA702-I&slash_SO
U4: ABLS-8.000MHZ-B2-T
U5: FT232RL; SSOP-28_5.3x10.2mm_P0.65mm
U6: CD74HC4514M96
U7: PTMUX1308QDYYRQ1
U8, U9, U10, U11, U12, U13: 74LVT573MTC
U14, U15, U16, U17: ULN2003AIDR
UART: USB_B; USB_B_TE_5787834_Vertical

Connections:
3.3V: 0.1uF1.2, C5.1, C7.1, C10.1, C13.2, C14.2, C15.2, C16.2, C17.2, C18.2, J3.3, J4.2, R1.1, R2.1, R6.2, R7.1, SW_1.1, SW_2.1, SW_3.1, SW_4.1, SW_5.1, TP_3.3V.1, U2.2 (OUT), U3.13 (VDD), U5.4 (VCCIO), U6.24 (VCC), U7.16 (VDD), U8.20 (VCC), U9.20 (VCC), U10.20 (VCC), U11.20 (VCC), U12.20 (VCC), U13.20 (VCC)
5V: C2.2, R3.2, TP_5V.1, U1.2 (OUT), U5.20 (VCC), UART.1 (VBUS)
12V: 12V.1, C1.1, C8.1, C19.2, C20.2, C21.2, C22.2, J7.1, J8.1, J9.1, J10.1, J11.1, J12.1, U1.3 (IN), U2.3 (IN), U14.9 (COM), U15.9 (COM), U16.9 (COM), U17.9 (COM)
A0: U3.17 (TCK/RP8/SCL1/OCM1B/CTED10/RB8), U6.2 (A0)
A1: U3.16 (RP7/OCM1A/CTED3/INT0/RB7), U6.3 (A1)
A2: U3.15 (PGC3/RP6/ASCL1/OCM1F/RB6), U6.21 (A2)
B1: J7.5, U14.13 (4C)
B2: J8.5, U15.16 (1C)
B3: J9.5, U15.12 (5C)
B4: J12.5, U16.15 (2C)
B5: J10.5, U16.11 (6C)
B6: J11.5, U17.14 (3C)
CS: J1.4, U3.18 (TDO/C1INC/C2INC/C3INC/TMPRN/RP9/SDA1/T1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)
D1: U3.24 (AN7/C1INC/RP13/OCM1D/CTPLS/RB13), U8.2 (D0), U9.2 (D0), U10.2 (D0), U11.2 (D0), U12.2 (D0), U13.2 (D0)
D2: U3.23 (AN8/LVDIN/RP12/RB12), U8.3 (D1), U9.3 (D1), U10.3 (D1), U11.3 (D1), U12.3 (D1), U13.3 (D1)
D3: U3.22 (PGC2/TMS/REFI1/RP11/CTED9/RB11), U8.4 (D2), U9.4 (D2), U10.4 (D2), U11.4 (D2), U12.4 (D2), U13.4 (D2)
D4: U3.21 (PGD2/TDI/RP10/OCM1C/CTED11/RB10), U8.5 (D3), U9.5 (D3), U10.5 (D3), U11.5 (D3), U12.5 (D3), U13.5 (D3)
D+: U5.15 (USBD+), UART.3 (D+)
D-: U5.16 (USBD-), UART.2 (D-)
E1: TP_E1.1, U6.11 (Y0), U8.11 (LE)
E2: TP_E2.1, U6.9 (Y1), U9.11 (LE)
E3: TP_E3.1, U6.10 (Y2), U10.11 (LE)
E4: TP_E4.1, U6.8 (Y3), U11.11 (LE)
E5: TP_E5.1, U6.7 (Y4), U12.11 (LE)
E6: TP_E6.1, U6.6 (Y5), U13.11 (LE)
GND: 0.1uF1.1, C1.2, C2.1, C3.1, C4.1, C5.2, C6.2, C7.2, C8.2, C9.1, C10.2, C12.1, C13.1, C14.1, C15.1, C16.1, C17.1, C18.1, C19.1, C20.1, C21.1, C22.1, GND.1, GND#2.1, GND#3.1, GND#4.1, J1.5, J4.3, R4.1, R5.1, R8.2, R9.2, R10.1, R11.1, R12.1, R13.1, R14.1, U3.8 (VSS), U3.19 (VSS), U5.7 (GND), U5.18 (GND), U5.21 (GND), U5.25 (AGND), U5.26 (TEST), U6.1 (LE_N), U6.12 (GND), U6.22 (A3), U6.23 (E_N), U7.2 (S6), U7.4 (S7), U7.5 (S5), U7.6 (EN), U7.8 (GND), U8.1 (OE_N), U8.6 (D4), U8.7 (D5), U8.8 (D6), U8.9 (D7), U8.10 (GND), U9.1 (OE_N), U9.6 (D4), U9.7 (D5), U9.8 (D6), U9.9 (D7), U9.10 (GND), U10.1 (OE_N), U10.6 (D4), U10.7 (D5), U10.8 (D6), U10.9 (D7), U10.10 (GND), U11.1 (OE_N), U11.6 (D4), U11.7 (D5), U11.8 (D6), U11.9 (D7), U11.10 (GND), U12.1 (OE_N), U12.6 (D4), U12.7 (D5), U12.8 (D6), U12.9 (D7), U12.10 (GND), U13.1 (OE_N), U13.6 (D4), U13.7 (D5), U13.8 (D6), U13.9 (D7), U13.10 (GND), U14.8 (E), U15.8 (E), U16.8 (E), U17.8 (E), UART.4 (GND)
M: U3.26 (AN9/C3INA/RP15/CTED6/RB15), U7.3 (D)
MISO: J1.3, U3.11 (SOSCI/RP4/RB4)
MOSI: J1.2, R2.2, U3.3 (VREF-/CVREF-/AN1/C3IND/RP27/CTED2/RA1)
unnamed: C6.1, J5.2
unnamed: C9.2, U5.17 (3V3OUT)
unnamed: C11.1, U3.28 (AVDD/VDD)
unnamed: C11.2, U3.27 (AVSS/VSS)
unnamed: C12.2, U3.20 (VCAP)
unnamed: J3.1, J4.1
unnamed: J3.2, J5.1, TP_MCLR.1, U3.1 (*MCLR)
unnamed: J5.3, R7.2
unnamed: R3.1, R4.2, U1.1 (ADJ)
unnamed: R5.2, R6.1, U2.1 (ADJ)
O1: J7.2, U14.16 (1C)
O2: J8.2, U14.12 (5C)
O3: J9.2, U15.15 (2C)
O4: J12.2, U15.11 (6C)
O5: J10.2, U16.14 (3C)
O6: J11.2, U16.10 (7C)
OSCI: C3.2, U3.9 (OSCI/CLKI/C1IND/RA2), U4.1
OSCO: C4.2, U3.10 (OSCO/CLKO/C2IND/RA3), U4.2
P1: R10.2, TP1.1.1, U7.13 (S0)
P2: R11.2, TP2.1.1, U7.14 (S1)
P3: R12.2, TP3.1.1, U7.15 (S2)
P4: R13.2, TP4.1.1, U7.12 (S3)
P5: R14.2, TP5.1.1, U7.1 (S4)
PGC: J4.5, R8.1, U3.5 (PGC1/AN1-/AN3/C2INA/RP1/CTED12/RB1)
PGD: J4.4, R9.1, U3.4 (PGD1/AN2/CTCMP/C2INB/RP0/RB0)
PI1: J7.4, U14.14 (3C)
PI2: J8.4, U14.10 (7C)
PI3: J9.4, U15.13 (4C)
PI4: J12.4, U16.16 (1C)
PI5: J10.4, U16.12 (5C)
PI6: J11.4, U17.15 (2C)
Q1.1: U8.19 (O0), U14.1 (1B)
Q1.2: U9.19 (O0), U14.5 (5B)
Q1.3: U10.19 (O0), U15.2 (2B)
Q1.4: U11.19 (O0), U15.6 (6B)
Q1.5: U12.19 (O0), U16.3 (3B)
Q1.6: U13.19 (O0), U16.7 (7B)
Q2.1: U8.18 (01), U14.2 (2B)
Q2.2: U9.18 (01), U14.6 (6B)
Q2.3: U10.18 (01), U15.3 (3B)
Q2.4: U11.18 (01), U15.7 (7B)
Q2.5: U12.18 (01), U16.4 (4B)
Q2.6: U13.18 (01), U17.1 (1B)
Q3.1: U8.17 (02), U14.3 (3B)
Q3.2: U9.17 (02), U14.7 (7B)
Q3.3: U10.17 (02), U15.4 (4B)
Q3.4: U11.17 (02), U16.1 (1B)
Q3.5: U12.17 (02), U16.5 (5B)
Q3.6: U13.17 (02), U17.2 (2B)
Q4.1: U8.16 (03), U14.4 (4B)
Q4.2: U9.16 (03), U15.1 (1B)
Q4.3: U10.16 (03), U15.5 (5B)
Q4.4: U11.16 (03), U16.2 (2B)
Q4.5: U12.16 (03), U16.6 (6B)
Q4.6: U13.16 (03), U17.3 (3B)
RX: TP_RX.1, U3.7 (AN5/C1INA/RP3/SCL2/CTED8/RB3), U5.1 (TXD)
S0: U3.25 (CVREF/AN6/C3INB/RP14/CTED5/RB14), U7.11 (A0)
S1: U3.12 (SOSCO/PWRLCLK/RA4), U7.10 (A1)
S2: U3.14 (PGD3/RP5/ASDA1/OCM1E/RB5), U7.9 (A2)
SCL: J1.1, R1.2, U3.2 (VREF+/CVREF+/AN0/C3INC/RP26/CTED1/RA0)
Y1: J7.3, U14.15 (2C)
Y2: J8.3, U14.11 (6C)
Y3: J9.3, U15.14 (3C)
Y4: J12.3, U15.10 (7C)
Y5: J10.3, U16.13 (4C)
Y6: J11.3, U17.16 (1C)
tx: TP_TX.1, U3.6 (AN4/C1INB/RP2/SDA2/CTED13/RB2), U5.5 (RXD)

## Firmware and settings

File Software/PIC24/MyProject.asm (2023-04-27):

MyProject_rotate:

;MyProject.c,12 :: 		static inline void rotate(int step, char s[], int left_right){ // left_right = 1 - lijevo, left_right = -1 - desno
;MyProject.c,13 :: 		i = 4*s[2] + 2*s[1] + s[0];
	ADD	W11, #2, W4
	MOV.B	[W4], W0
	ZE	W0, W0
	SL	W0, #2, W1
	ADD	W11, #1, W3
	MOV.B	[W3], W0
	ZE	W0, W0
	SL	W0, #1, W0
	ADD	W1, W0, W2
	ZE	[W11], W1
	MOV	#lo_addr(_i), W0
	ADD	W2, W1, [W0]
;MyProject.c,14 :: 		LATB.F6 = s[2];
	MOV.B	[W4], W0
	BTSS	W0, #0
	BCLR.B	LATB, #6
	BTSC	W0, #0
	BSET.B	LATB, #6
;MyProject.c,15 :: 		LATB.F7 = s[1];
	MOV.B	[W3], W0
	BTSS	W0, #0
	BCLR.B	LATB, #7
	BTSC	W0, #0
	BSET.B	LATB, #7
;MyProject.c,16 :: 		LATB.F8 = s[0];
	MOV.B	[W11], W0
	BTSS	W0, #0
	BCLR	LATB, #8
	BTSC	W0, #0
	BSET	LATB, #8
;MyProject.c,17 :: 		while(step > 0){
L_MyProject_rotate0:
	CP	W10, #0
	BRA GT	L_MyProject_rotate107
	GOTO	L_MyProject_rotate1
L_MyProject_rotate107:
;MyProject.c,18 :: 		LATB.F13 = lookup[indexes[i]][0];
	MOV	#lo_addr(_indexes), W1
	MOV	#lo_addr(_i), W0
	ADD	W1, [W0], W2
	MOV.B	[W2], W0
	SE	W0, W0
	SL	W0, #3, W1
	MOV	#lo_addr(_lookup), W0
	ADD	W0, W1, W1
	MOV	#___Lib_System_DefaultPage, W0
	MOV	WREG, 50
	MOV	[W1], W0
	BTSS	W0, #0
	BCLR	LATB, #13
	BTSC	W0, #0
	BSET	LATB, #13
;MyProject.c,19 :: 		LATB.F12 = lookup[indexes[i]][1];
	MOV.B	[W2], W0
	SE	W0, W0
	SL	W0, #3, W1
	MOV	#lo_addr(_lookup), W0
	ADD	W0, W1, W0
	ADD	W0, #2, W1
	MOV	#___Lib_System_DefaultPage, W0
	MOV	WREG, 50
	MOV	[W1], W0
	BTSS	W0, #0
	BCLR	LATB, #12
	BTSC	W0, #0
	BSET	LATB, #12
;MyProject.c,20 :: 		LATB.F11 = lookup[indexes[i]][2];
	MOV.B	[W2], W0
	SE	W0, W0
	SL	W0, #3, W1
	MOV	#lo_addr(_lookup), W0
	ADD	W0, W1, W0
	ADD	W0, #4, W1
	MOV	#___Lib_System_DefaultPage, W0
	MOV	WREG, 50
	MOV	[W1], W0
	BTSS	W0, #0
	BCLR	LATB, #11
	BTSC	W0, #0
	BSET	LATB, #11
;MyProject.c,21 :: 		LATB.F10 = lookup[indexes[i]][3];
	MOV.B	[W2], W0
	SE	W0, W0
	SL	W0, #3, W1
	MOV	#lo_addr(_lookup), W0
	ADD	W0, W1, W0
	ADD	W0, #6, W1
	MOV	#___Lib_System_DefaultPage, W0
	MOV	WREG, 50
	MOV	[W1], W0
	BTSS	W0, #0
	BCLR	LATB, #10
	BTSC	W0, #0
	BSET	LATB, #10
;MyProject.c,22 :: 		step--;
	SUB	W10, #1, W0
	MOV	W0, W10
;MyProject.c,23 :: 		indexes[i] += left_right;
	SE	[W2], W0
	ADD	W0, W12, W0
	MOV.B	W0, [W2]
;MyProject.c,24 :: 		if (indexes[i] >= 8 && left_right == 1)
	MOV	#lo_addr(_indexes), W1
	MOV	#lo_addr(_i), W0
	ADD	W1, [W0], W0
	MOV.B	[W0], W0
	CP.B	W0, #8
	BRA GE	L_MyProject_rotate108
	GOTO	L_MyProject_rotate79
L_MyProject_rotate108:
	CP	W12, #1
	BRA Z	L_MyProject_rotate109
	GOTO	L_MyProject_rotate78
L_MyProject_rotate109:
L_MyProject_rotate77:
;MyProject.c,25 :: 		indexes[i] = 0;
	MOV	#lo_addr(_indexes), W1
	MOV	#lo_addr(_i), W0
	ADD	W1, [W0], W1
	CLR	W0
	MOV.B	W0, [W1]
;MyProject.c,24 :: 		if (indexes[i] >= 8 && left_right == 1)
L_MyProject_rotate79:
L_MyProject_rotate78:
;MyProject.c,26 :: 		if (indexes[i] < 0  && left_right == -1)
	MOV	#lo_addr(_indexes), W1
	MOV	#lo_addr(_i), W0
	ADD	W1, [W0], W0
	MOV.B	[W0], W0
	CP.B	W0, #0
	BRA LT	L_MyProject_rotate110
	GOTO	L_MyProject_rotate81
L_MyProject_rotate110:
	MOV	#65535, W0
	CP	W12, W0
	BRA Z	L_MyProject_rotate111
	GOTO	L_MyProject_rotate80
L_MyProject_rotate111:
L_MyProject_rotate76:
;MyProject.c,27 :: 		indexes[i] = 7;
	MOV	#lo_addr(_indexes), W1
	MOV	#lo_addr(_i), W0
	ADD	W1, [W0], W1
	MOV.B	#7, W0
	MOV.B	W0, [W1]
;MyProject.c,26 :: 		if (indexes[i] < 0  && left_right == -1)
L_MyProject_rotate81:
L_MyProject_rotate80:
;MyProject.c,28 :: 		Delay_us(pauza);
	MOV	#1466, W7
L_MyProject_rotate8:
	DEC	W7
	BRA NZ	L_MyProject_rotate8
	NOP
	NOP
;MyProject.c,29 :: 		}
	GOTO	L_MyProject_rotate0
L_MyProject_rotate1:
;MyProject.c,30 :: 		LATB.F13 = 0;
	BCLR	LATB, #13
;MyProject.c,31 :: 		LATB.F12 = 0;
	BCLR	LATB, #12
;MyProject.c,32 :: 		LATB.F11 = 0;
	BCLR	LATB, #11
;MyProject.c,33 :: 		LATB.F10 = 0;
	BCLR	LATB, #10
;MyProject.c,34 :: 		LATB.F6 = 1;
	BSET.B	LATB, #6
;MyProject.c,35 :: 		LATB.F7 = 1;
	BSET.B	LATB, #7
;MyProject.c,36 :: 		LATB.F8 = 1;
	BSET	LATB, #8
;MyProject.c,37 :: 		}
L_end_rotate:
	RETURN
; end of MyProject_rotate

_uart_interrupt:
	PUSH	DSWPAG
	PUSH	50
	PUSH	RCOUNT
	PUSH	W0
	MOV	#2, W0
	REPEAT	#12
	PUSH	[W0++]

;MyProject.c,39 :: 		void uart_interrupt() iv IVT_ADDR_U1RXINTERRUPT ics ICS_AUTO {
;MyProject.c,40 :: 		IFS0bits.U1RXIF = 0;
	BCLR	IFS0bits, #11
;MyProject.c,41 :: 		uart_ch = UART1_Read();
	CALL	_UART1_Read
	MOV	#lo_addr(_uart_ch), W1
	MOV.B	W0, [W1]
;MyProject.c,42 :: 		if(uart_ch == 'q'){
	MOV.B	#113, W1
	CP.B	W0, W1
	BRA Z	L__uart_interrupt113
	GOTO	L_uart_interrupt10
L__uart_interrupt113:
;MyProject.c,43 :: 		m = 0;
	CLR	W0
	MOV	W0, _m
;MyProject.c,44 :: 		flag = 1;
	MOV	#1, W0
	MOV	W0, _flag
;MyProject.c,45 :: 		}
	GOTO	L_uart_interrupt11
L_uart_interrupt10:
;MyProject.c,47 :: 		out[m] = uart_ch;
	MOV	#lo_addr(_out), W1
	MOV	#lo_addr(_m), W0
	ADD	W1, [W0], W1
	MOV	#lo_addr(_uart_ch), W0
	MOV.B	[W0], [W1]
;MyProject.c,48 :: 		m++;
	MOV	#1, W1
	MOV	#lo_addr(_m), W0
	ADD	W1, [W0], [W0]
;MyProject.c,49 :: 		}
L_uart_interrupt11:
;MyProject.c,50 :: 		}
L_end_uart_interrupt:
	MOV	#26, W0
	REPEAT	#12
	POP	[W0--]
	POP	W0
	POP	RCOUNT
	POP	50
	POP	DSWPAG
	RETFIE
; end of _uart_interrupt

_calibration:

;MyProject.c,52 :: 		void calibration(){
;MyProject.c,53 :: 		LATB.F6 = 1;
	PUSH	W10
	PUSH	W11
	PUSH	W12
	BSET.B	LATB, #6
;MyProject.c,54 :: 		LATB.F7 = 0;
	BCLR.B	LATB, #7
;MyProject.c,55 :: 		LATB.F8 = 0;
	BCLR	LATB, #8
;MyProject.c,56 :: 		while(1){
L_calibration12:
;MyProject.c,57 :: 		if(PORTB.F5 == 1)
	BTSS	PORTB, #5
	GOTO	L_calibration14
;MyProject.c,58 :: 		break;
	GOTO	L_calibration13
L_calibration14:
;MyProject.c,59 :: 		LATB.F13 = lookup[indexes[4]][0];
	MOV	#lo_addr(_indexes+4), W0
	SE	[W0], W0
	SL	W0, #3, W1
	MOV	#lo_addr(_lookup), W0
	ADD	W0, W1, W2
	MOV	#___Lib_System_DefaultPage, W0
	MOV	WREG, 50
	MOV	[W2], W0
	BTSS	W0, #0
	BCLR	LATB, #13
	BTSC	W0, #0
	BSET	LATB, #13
;MyProject.c,60 :: 		LATB.F12 = lookup[indexes[4]][1];
	ADD	W2, #2, W1
	MOV	#___Lib_System_DefaultPage, W0
	MOV	WREG, 50
	MOV	[W1], W0
	BTSS	W0, #0
	BCLR	LATB, #12
	BTSC	W0, #0
	BSET	LATB, #12
;MyProject.c,61 :: 		LATB.F11 = lookup[indexes[4]][2];
	ADD	W2, #4, W1
	MOV	#___Lib_System_DefaultPage, W0
	MOV	WREG, 50
	MOV	[W1], W0
	BTSS	W0, #0
	BCLR	LATB, #11
	BTSC	W0, #0
	BSET	LATB, #11
;MyProject.c,62 :: 		LATB.F10 = lookup[indexes[4]][3];
	ADD	W2, #6, W1
	MOV	#___Lib_System_DefaultPage, W0
	MOV	WREG, 50
	MOV	[W1], W0
	BTSS	W0, #0
	BCLR	LATB, #10
	BTSC	W0, #0
	BSET	LATB, #10
;MyProject.c,63 :: 		Delay_us(pauza);
	MOV	#1466, W7
L_calibration15:
	DEC	W7
	BRA NZ	L_calibration15
	NOP
	NOP
;MyProject.c,64 :: 		indexes[4]--;
	MOV.B	#1, W1
	MOV	#lo_addr(_indexes+4), W0
	SUBR.B	W1, [W0], [W0]
;MyProject.c,65 :: 		if (indexes[4] < 0)
	MOV	#lo_addr(_indexes+4), W0
	MOV.B	[W0], W0
	CP.B	W0, #0
	BRA LT	L__calibration115
	GOTO	L_calibration17
L__calibration115:
;MyProject.c,66 :: 		indexes[4] = 7;
	MOV	#lo_addr(_indexes+4), W1
	MOV.B	#7, W0
	MOV.B	W0, [W1]
L_calibration17:
;MyProject.c,67 :: 		}
	GOTO	L_calibration12
L_calibration13:
;MyProject.c,68 :: 		LATB.F13 = 0;
	BCLR	LATB, #13
;MyProject.c,69 :: 		LATB.F12 = 0;
	BCLR	LATB, #12
;MyProject.c,70 :: 		LATB.F11 = 0;
	BCLR	LATB, #11
;MyProject.c,71 :: 		LATB.F10 = 0;
	BCLR	LATB, #10
;MyProject.c,72 :: 		step_code[0] = 0;
	MOV	#lo_addr(_step_code), W1
	CLR	W0
	MOV.B	W0, [W1]
;MyProject.c,73 :: 		step_code[1] = 0;
	MOV	#lo_addr(_step_code+1), W1
	CLR	W0
	MOV.B	W0, [W1]
;MyProject.c,74 :: 		step_code[2] = 1;
	MOV	#lo_addr(_step_code+2), W1
	MOV.B	#1, W0
	MOV.B	W0, [W1]
;MyProject.c,75 :: 		rotate(910, step_code, 1);
	MOV	#1, W12
	MOV	#lo_addr(_step_code), W11
	MOV	#910, W10
	CALL	MyProject_rotate
;MyProject.c,76 :: 		LATB.F6 = 0;
	BCLR.B	LATB, #6
;MyProject.c,77 :: 		LATB.F7 = 0;
	BCLR.B	LATB, #7
;MyProject.c,78 :: 		LATB.F8 = 1;
	BSET	LATB, #8
;MyProject.c,79 :: 		while(1){
L_calibration18:
;MyProject.c,80 :: 		if(PORTB.F15 == 1)
	BTSS	PORTB, #15
	GOTO	L_calibration20
;MyProject.c,81 :: 		break;
	GOTO	L_calibration19
L_calibration20:
;MyProject.c,82 :: 		LATB.F13 = lookup[indexes[1]][0];
	MOV	#lo_addr(_indexes+1), W0
	SE	[W0], W0
	SL	W0, #3, W1
	MOV	#lo_addr(_lookup), W0
	ADD	W0, W1, W2
	MOV	#___Lib_System_DefaultPage, W0
	MOV	WREG, 50
	MOV	[W2], W0
	BTSS	W0, #0
	BCLR	LATB, #13
	BTSC	W0, #0
	BSET	LATB, #13
;MyProject.c,83 :: 		LATB.F12 = lookup[indexes[1]][1];
	ADD	W2, #2, W1
	MOV	#___Lib_System_DefaultPage, W0
	MOV	WREG, 50
	MOV	[W1], W0
	BTSS	W0, #0
	BCLR	LATB, #12
	BTSC	W0, #0
	BSET	LATB, #12
;MyProject.c,84 :: 		LATB.F11 = lookup[indexes[1]][2];
	ADD	W2, #4, W1
	MOV	#___Lib_System_DefaultPage, W0
	MOV	WREG, 50
	MOV	[W1], W0
	BTSS	W0, #0
	BCLR	LATB, #11
	BTSC	W0, #0
	BSET	LATB, #11
;MyProject.c,85 :: 		LATB.F10 = lookup[indexes[1]][3];
	ADD	W2, #6, W1
	MOV	#___Lib_System_DefaultPage, W0
	MOV	WREG, 50
	MOV	[W1], W0
	BTSS	W0, #0
	BCLR	LATB, #10
	BTSC	W0, #0
	BSET	LATB, #10
;MyProject.c,86 :: 		Delay_us(pauza);
	MOV	#1466, W7
L_calibration21:
	DEC	W7
	BRA NZ	L_calibration21
	NOP
	NOP
;MyProject.c,87 :: 		indexes[1]--;
	MOV.B	#1, W1
	MOV	#lo_addr(_indexes+1), W0
	SUBR.B	W1, [W0], [W0]
;MyProject.c,88 :: 		if (indexes[1] < 0)
	MOV	#lo_addr(_indexes+1), W0
	MOV.B	[W0], W0
	CP.B	W0, #0
	BRA LT	L__calibration116
	GOTO	L_calibration23
L__calibration116:
;MyProject.c,89 :: 		indexes[1] = 7;
	MOV	#lo_addr(_indexes+1), W1
	MOV.B	#7, W0
	MOV.B	W0, [W1]
L_calibration23:
;MyProject.c,90 :: 		}
	GOTO	L_calibration18
L_calibration19:
;MyProject.c,91 :: 		LATB.F13 = 0;
	BCLR	LATB, #13
;MyProject.c,92 :: 		LATB.F12 = 0;
	BCLR	LATB, #12
;MyProject.c,93 :: 		LATB.F11 = 0;
	BCLR	LATB, #11
;MyProject.c,94 :: 		LATB.F10 = 0;
	BCLR	LATB, #10
;MyProject.c,95 :: 		step_code[0] = 1;
	MOV	#lo_addr(_step_code), W1
	MOV.B	#1, W0
	MOV.B	W0, [W1]
;MyProject.c,96 :: 		step_code[1] = 0;
	MOV	#lo_addr(_step_code+1), W1
	CLR	W0
	MOV.B	W0, [W1]
;MyProject.c,97 :: 		step_code[2] = 0;
	MOV	#lo_addr(_step_code+2), W1
	CLR	W0
	MOV.B	W0, [W1]
;MyProject.c,98 :: 		rotate(3000, step_code, 1);
	MOV	#1, W12
	MOV	#lo_addr(_step_code), W11
	MOV	#3000, W10
	CALL	MyProject_rotate
;MyProject.c,99 :: 		}
L_end_calibration:
	POP	W12
	POP	W11
	POP	W10
	RETURN
; end of _calibration

_main:
	MOV	#2048, W15
	MOV	#6142, W0
	MOV	WREG, 32
	MOV	#1, W0
	MOV	WREG, 50
	MOV	#4, W0
	IOR	68

;MyProject.c,101 :: 		void main() {
;MyProject.c,102 :: 		OSCDIVbits.DIV = 0;
	PUSH	W10
	PUSH	W11
	PUSH	W12
	MOV	OSCDIVbits, W1
	MOV	#32768, W0
	AND	W1, W0, W0
	MOV	WREG, OSCDIVbits
;MyProject.c,104 :: 		ANSA = 0;
	CLR	ANSA
;MyProject.c,105 :: 		ANSB = 0;
	CLR	ANSB
;MyProject.c,107 :: 		TRISB = 0b0000010000000001;
	MOV	#1025, W0
	MOV	WREG, TRISB
;MyProject.c,108 :: 		TRISA = 0b00000;
	CLR	TRISA
;MyProject.c,110 :: 		ODCA = 0;
	CLR	ODCA
;MyProject.c,111 :: 		ODCB = 0;
	CLR	ODCB
;MyProject.c,113 :: 		LATA = 0;
	CLR	LATA
;MyProject.c,114 :: 		LATB = 0;
	CLR	LATB
;MyProject.c,116 :: 		Unlock_IOLOCK();
	CALL	_Unlock_IOLOCK
;MyProject.c,117 :: 		PPS_Mapping_NoLock(3, _INPUT, _U1RX);
	MOV.B	#19, W12
	MOV.B	#1, W11
	MOV.B	#3, W10
	CALL	_PPS_Mapping_NoLock
;MyProject.c,118 :: 		PPS_Mapping_NoLock(2, _OUTPUT, _U1TX);
	MOV.B	#3, W12
	CLR	W11
	MOV.B	#2, W10
	CALL	_PPS_Mapping_NoLock
;MyProject.c,119 :: 		Lock_IOLOCK();
	CALL	_Lock_IOLOCK
;MyProject.c,121 :: 		IEC0bits.U1RXIE = 1;
	BSET	IEC0bits, #11
;MyProject.c,122 :: 		IFS0bits.U1RXIF = 0;
	BCLR	IFS0bits, #11
;MyProject.c,124 :: 		UART1_Init(9600);
	MOV	#9600, W10
	MOV	#0, W11
	CALL	_UART1_Init
;MyProject.c,125 :: 		Delay_ms(100);
	MOV	#3, W8
	MOV	#2261, W7
L_main24:
	DEC	W7
	BRA NZ	L_main24
	DEC	W8
	BRA NZ	L_main24
;MyProject.c,126 :: 		calibration();
	CALL	_calibration
;MyProject.c,127 :: 		LATB.F6 = 1;
	BSET.B	LATB, #6
;MyProject.c,128 :: 		LATB.F7 = 1;
	BSET.B	LATB, #7
;MyProject.c,129 :: 		LATB.F8 = 1;
	BSET	LATB, #8
;MyProject.c,130 :: 		Delay_ms(100);
	MOV	#3, W8
	MOV	#2261, W7
L_main26:
	DEC	W7
	BRA NZ	L_main26
	DEC	W8
	BRA NZ	L_main26
;MyProject.c,131 :: 		while(1) {
L_main28:
;MyProject.c,132 :: 		if(flag == 1){
	MOV	_flag, W0
	CP	W0, #1
	BRA Z	L__main118
	GOTO	L_main30
L__main118:
;MyProject.c,133 :: 		flag = 0;
	CLR	W0
	MOV	W0, _flag
;MyProject.c,134 :: 		if(out[0] == 'A'){
	MOV	#lo_addr(_out), W0
	MOV.B	[W0], W1
	MOV.B	#65, W0
	CP.B	W1, W0
	BRA Z	L__main119
	GOTO	L_main31
L__main119:
;MyProject.c,135 :: 		step_code[0] = 0;
	MOV	#lo_addr(_step_code), W1
	CLR	W0
	MOV.B	W0, [W1]
;MyProject.c,136 :: 		step_code[1] = 0;
	MOV	#lo_addr(_step_code+1), W1
	CLR	W0
	MOV.B	W0, [W1]
;MyProject.c,137 :: 		step_code[2] = 0;
	MOV	#lo_addr(_step_code+2), W1
	CLR	W0
	MOV.B	W0, [W1]
;MyProject.c,138 :: 		rotate(20, step_code, 1);
	MOV	#1, W12
	MOV	#lo_addr(_step_code), W11
	MOV	#20, W10
	CALL	MyProject_rotate
;MyProject.c,139 :: 		}
	GOTO	L_main32
L_main31:
;MyProject.c,140 :: 		else if(out[0] == 'D'){
	MOV	#lo_addr(_out), W0
	MOV.B	[W0], W1
	MOV.B	#68, W0
	CP.B	W1, W0
	BRA Z	L__main120
	GOTO	L_main33
L__main120:
;MyProject.c,141 :: 		step_code[0] = 0;
	MOV	#lo_addr(_step_code), W1
	CLR	W0
	MOV.B	W0, [W1]
;MyProject.c,142 :: 		step_code[1] = 0;
	MOV	#lo_addr(_step_code+1), W1
	CLR	W0
	MOV.B	W0, [W1]
;MyProject.c,143 :: 		step_code[2] = 0;
	MOV	#lo_addr(_step_code+2), W1
	CLR	W0
	MOV.B	W0, [W1]
;MyProject.c,144 :: 		rotate(20, step_code, -1);
	MOV	#65535, W12
	MOV	#lo_addr(_step_code), W11
	MOV	#20, W10
	CALL	MyProject_rotate
;MyProject.c,145 :: 		}
	GOTO	L_main34
L_main33:
;MyProject.c,146 :: 		else if(out[0] == 'J'){
	MOV	#lo_addr(_out), W0
	MOV.B	[W0], W1
	MOV.B	#74, W0
	CP.B	W1, W0
	BRA Z	L__main121
	GOTO	L_main35
L__main121:
;MyProject.c,147 :: 		step_code[0] = 1;
	MOV	#lo_addr(_step_code), W1
	MOV.B	#1, W0
	MOV.B	W0, [W1]
;MyProject.c,148 :: 		step_code[1] = 0;
	MOV	#lo_addr(_step_code+1), W1
	CLR	W0
	MOV.B	W0, [W1]
;MyProject.c,149 :: 		step_code[2] = 1;
	MOV	#lo_addr(_step_code+2), W1
	MOV.B	#1, W0
	MOV.B	W0, [W1]
;MyProject.c,150 :: 		rotate(20, step_code, 1);
	MOV	#1, W12
	MOV	#lo_addr(_step_code), W11
	MOV	#20, W10
	CALL	MyProject_rotate
;MyProject.c,151 :: 		}
	GOTO	L_main36
L_main35:
;MyProject.c,152 :: 		else if(out[0] == 'L'){
	MOV	#lo_addr(_out), W0
	MOV.B	[W0], W1
	MOV.B	#76, W0
	CP.B	W1, W0
	BRA Z	L__main122
	GOTO	L_main37
L__main122:
;MyProject.c,153 :: 		step_code[0] = 1;
	MOV	#lo_addr(_step_code), W1
	MOV.B	#1, W0
	MOV.B	W0, [W1]
;MyProject.c,154 :: 		step_code[1] = 0;
	MOV	#lo_addr(_step_code+1), W1
	CLR	W0
	MOV.B	W0, [W1]
;MyProject.c,155 :: 		step_code[2] = 1;
	MOV	#lo_addr(_step_code+2), W1
	MOV.B	#1, W0
	MOV.B	W0, [W1]
;MyProject.c,156 :: 		rotate(20, step_code, -1);
	MOV	#65535, W12
	MOV	#lo_addr(_step_code), W11
	MOV	#20, W10
	CALL	MyProject_rotate
;MyProject.c,157 :: 		}
	GOTO	L_main38
L_main37:
;MyProject.c,158 :: 		else if(out[0] == 'O' && out[1] == 'L'){
	MOV	#lo_addr(_out), W0
	MOV.B	[W0], W1
	MOV.B	#79, W0
	CP.B	W1, W0
	BRA Z	L__main123
	GOTO	L__main91
L__main123:
	MOV	#lo_addr(_out+1), W0
	MOV.B	[W0], W1
	MOV.B	#76, W0
	CP.B	W1, W0
	BRA Z	L__main124
	GOTO	L__main90
L__main124:
L__main89:
;MyProject.c,159 :: 		korak1 = atoi(out+2);
	MOV	#lo_addr(_out+2), W10
	CALL	_atoi
	MOV	W0, _korak1
;MyProject.c,160 :: 		step_code[0] = 0;
	MOV	#lo_addr(_step_code), W2
	CLR	W1
	MOV.B	W1, [W2]
;MyProject.c,161 :: 		step_code[1] = 1;
	MOV	#lo_addr(_step_code+1), W2
	MOV.B	#1, W1
	MOV.B	W1, [W2]
;MyProject.c,162 :: 		step_code[2] = 0;
	MOV	#lo_addr(_step_code+2), W2
	CLR	W1
	MOV.B	W1, [W2]
;MyProject.c,163 :: 		rotate(korak1, step_code, 1);
	MOV	#1, W12
	MOV	#lo_addr(_step_code), W11
	MOV	W0, W10
	CALL	MyProject_rotate
;MyProject.c,164 :: 		UART1_Write('1');
	MOV	#49, W10
	CALL	_UART1_Write
;MyProject.c,165 :: 		}
	GOTO	L_main42
;MyProject.c,158 :: 		else if(out[0] == 'O' && out[1] == 'L'){
L__main91:
L__main90:
;MyProject.c,166 :: 		else if(out[0] == 'O' && out[1] == 'D'){
	MOV	#lo_addr(_out), W0
	MOV.B	[W0], W1
	MOV.B	#79, W0
	CP.B	W1, W0
	BRA Z	L__main125
	GOTO	L__main93
L__main125:
	MOV	#lo_addr(_out+1), W0
	MOV.B	[W0], W1
	MOV.B	#68, W0
	CP.B	W1, W0
	BRA Z	L__main126
	GOTO	L__main92
L__main126:
L__main88:
;MyProject.c,167 :: 		korak1 = atoi(out+2);
	MOV	#lo_addr(_out+2), W10
	CALL	_atoi
	MOV	W0, _korak1
;MyProject.c,168 :: 		step_code[0] = 0;
	MOV	#lo_addr(_step_code), W2
	CLR	W1
	MOV.B	W1, [W2]
;MyProject.c,169 :: 		step_code[1] = 1;
	MOV	#lo_addr(_step_code+1), W2
	MOV.B	#1, W1
	MOV.B	W1, [W2]
;MyProject.c,170 :: 		step_code[2] = 0;
	MOV	#lo_addr(_step_code+2), W2
	CLR	W1
	MOV.B	W1, [W2]
;MyProject.c,171 :: 		rotate(korak1, step_code, -1);
	MOV	#65535, W12
	MOV	#lo_addr(_step_code), W11
	MOV	W0, W10
	CALL	MyProject_rotate
;MyProject.c,172 :: 		UART1_Write('1');
	MOV	#49, W10
	CALL	_UART1_Write
;MyProject.c,173 :: 		}
	GOTO	L_main46
;MyProject.c,166 :: 		else if(out[0] == 'O' && out[1] == 'D'){
L__main93:
L__main92:
;MyProject.c,174 :: 		else if(out[0] == 'K' && out[1] == 'A'){
	MOV	#lo_addr(_out), W0
	MOV.B	[W0], W1
	MOV.B	#75, W0
	CP.B	W1, W0
	BRA Z	L__main127
	GOTO	L__main95
L__main127:
	MOV	#lo_addr(_out+1), W0
	MOV.B	[W0], W1
	MOV.B	#65, W0
	CP.B	W1, W0
	BRA Z	L__main128
	GOTO	L__main94
L__main128:
L__main87:
;MyProject.c,175 :: 		korak1 = atoi(out+2);
	MOV	#lo_addr(_out+2), W10
	CALL	_atoi
	MOV	W0, _korak1
;MyProject.c,176 :: 		step_code[0] = 1;
	MOV	#lo_addr(_step_code), W2
	MOV.B	#1, W1
	MOV.B	W1, [W2]
;MyProject.c,177 :: 		step_code[1] = 0;
	MOV	#lo_addr(_step_code+1), W2
	CLR	W1
	MOV.B	W1, [W2]
;MyProject.c,178 :: 		step_code[2] = 0;
	MOV	#lo_addr(_step_code+2), W2
	CLR	W1
	MOV.B	W1, [W2]
;MyProject.c,179 :: 		rotate(korak1, step_code, -1);
	MOV	#65535, W12
	MOV	#lo_addr(_step_code), W11
	MOV	W0, W10
	CALL	MyProject_rotate
;MyProject.c,180 :: 		}
	GOTO	L_main50
;MyProject.c,174 :: 		else if(out[0] == 'K' && out[1] == 'A'){
L__main95:
L__main94:
;MyProject.c,181 :: 		else if(out[0] == 'N' && out[1] == '1'){
	MOV	#lo_addr(_out), W0
	MOV.B	[W0], W1
	MOV.B	#78, W0
	CP.B	W1, W0
	BRA Z	L__main129
	GOTO	L__main97
L__main129:
	MOV	#lo_addr(_out+1), W0
	MOV.B	[W0], W1
	MOV.B	#49, W0
	CP.B	W1, W0
	BRA Z	L__main130
	GOTO	L__main96
L__main130:
L__main86:
;MyProject.c,182 :: 		step_code[0] = 1;
	MOV	#lo_addr(_step_code), W1
	MOV.B	#1, W0
	MOV.B	W0, [W1]
;MyProject.c,183 :: 		step_code[1] = 1;
	MOV	#lo_addr(_step_code+1), W1
	MOV.B	#1, W0
	MOV.B	W0, [W1]
;MyProject.c,184 :: 		step_code[2] = 0;
	MOV	#lo_addr(_step_code+2), W1
	CLR	W0
	MOV.B	W0, [W1]
;MyProject.c,185 :: 		rotate(2276, step_code, 1); // 40 stepeni
	MOV	#1, W12
	MOV	#lo_addr(_step_code), W11
	MOV	#2276, W10
	CALL	MyProject_rotate
;MyProject.c,186 :: 		UART1_Write('1');
	MOV	#49, W10
	CALL	_UART1_Write
;MyProject.c,187 :: 		}
	GOTO	L_main54
;MyProject.c,181 :: 		else if(out[0] == 'N' && out[1] == '1'){
L__main97:
L__main96:
;MyProject.c,188 :: 		else if(out[0] == 'N' && out[1] == '2'){
	MOV	#lo_addr(_out), W0
	MOV.B	[W0], W1
	MOV.B	#78, W0
	CP.B	W1, W0
	BRA Z	L__main131
	GOTO	L__main99
L__main131:
	MOV	#lo_addr(_out+1), W0
	MOV.B	[W0], W1
	MOV.B	#50, W0
	CP.B	W1, W0
	BRA Z	L__main132
	GOTO	L__main98
L__main132:
L__main85:
;MyProject.c,189 :: 		step_code[0] = 1;
	MOV	#lo_addr(_step_code), W1
	MOV.B	#1, W0
	MOV.B	W0, [W1]
;MyProject.c,190 :: 		step_code[1] = 1;
	MOV	#lo_addr(_step_code+1), W1
	MOV.B	#1, W0
	MOV.B	W0, [W1]
;MyProject.c,191 :: 		step_code[2] = 0;
	MOV	#lo_addr(_step_code+2), W1
	CLR	W0
	MOV.B	W0, [W1]
;MyProject.c,192 :: 		rotate(2845, step_code, 1); // 50 stepeni
	MOV	#1, W12
	MOV	#lo_addr(_step_code), W11
	MOV	#2845, W10
	CALL	MyProject_rotate
;MyProject.c,193 :: 		UART1_Write('1');
	MOV	#49, W10
	CALL	_UART1_Write
;MyProject.c,194 :: 		}
	GOTO	L_main58
;MyProject.c,188 :: 		else if(out[0] == 'N' && out[1] == '2'){
L__main99:
L__main98:
;MyProject.c,195 :: 		else if(out[0] == 'N' && out[1] == '3'){
	MOV	#lo_addr(_out), W0
	MOV.B	[W0], W1
	MOV.B	#78, W0
	CP.B	W1, W0
	BRA Z	L__main133
	GOTO	L__main101
L__main133:
	MOV	#lo_addr(_out+1), W0
	MOV.B	[W0], W1
	MOV.B	#51, W0
	CP.B	W1, W0
	BRA Z	L__main134
	GOTO	L__main100
L__main134:
L__main84:
;MyProject.c,196 :: 		step_code[0] = 1;
	MOV	#lo_addr(_step_code), W1
	MOV.B	#1, W0
	MOV.B	W0, [W1]
;MyProject.c,197 :: 		step_code[1] = 1;
	MOV	#lo_addr(_step_code+1), W1
	MOV.B	#1, W0
	MOV.B	W0, [W1]
;MyProject.c,198 :: 		step_code[2] = 0;
	MOV	#lo_addr(_step_code+2), W1
	CLR	W0
	MOV.B	W0, [W1]
;MyProject.c,199 :: 		rotate(3840, step_code, 1); // 67.5 stepeni
	MOV	#1, W12
	MOV	#lo_addr(_step_code), W11
	MOV	#3840, W10
	CALL	MyProject_rotate
;MyProject.c,200 :: 		UART1_Write('1');
	MOV	#49, W10
	CALL	_UART1_Write
;MyProject.c,201 :: 		}
	GOTO	L_main62
;MyProject.c,195 :: 		else if(out[0] == 'N' && out[1] == '3'){
L__main101:
L__main100:
;MyProject.c,202 :: 		else if(out[0] == 'N' && out[1] == '4'){
	MOV	#lo_addr(_out), W0
	MOV.B	[W0], W1
	MOV.B	#78, W0
	CP.B	W1, W0
	BRA Z	L__main135
	GOTO	L__main103
L__main135:
	MOV	#lo_addr(_out+1), W0
	MOV.B	[W0], W1
	MOV.B	#52, W0
	CP.B	W1, W0
	BRA Z	L__main136
	GOTO	L__main102
L__main136:
L__main83:
;MyProject.c,203 :: 		step_code[0] = 1;
	MOV	#lo_addr(_step_code), W1
	MOV.B	#1, W0
	MOV.B	W0, [W1]
;MyProject.c,204 :: 		step_code[1] = 1;
	MOV	#lo_addr(_step_code+1), W1
	MOV.B	#1, W0
	MOV.B	W0, [W1]
;MyProject.c,205 :: 		step_code[2] = 0;
	MOV	#lo_addr(_step_code+2), W1
	CLR	W0
	MOV.B	W0, [W1]
;MyProject.c,206 :: 		rotate(4552, step_code, 1); // 80 stepeni
	MOV	#1, W12
	MOV	#lo_addr(_step_code), W11
	MOV	#4552, W10
	CALL	MyProject_rotate
;MyProject.c,207 :: 		UART1_Write('1');
	MOV	#49, W10
	CALL	_UART1_Write
;MyProject.c,208 :: 		}
	GOTO	L_main66
;MyProject.c,202 :: 		else if(out[0] == 'N' && out[1] == '4'){
L__main103:
L__main102:
;MyProject.c,209 :: 		else if(out[0] == 'N' && out[1] == '5'){
	MOV	#lo_addr(_out), W0
	MOV.B	[W0], W1
	MOV.B	#78, W0
	CP.B	W1, W0
	BRA Z	L__main137
	GOTO	L__main105
L__main137:
	MOV	#lo_addr(_out+1), W0
	MOV.B	[W0], W1
	MOV.B	#53, W0
	CP.B	W1, W0
	BRA Z	L__main138
	GOTO	L__main104
L__main138:
L__main82:
;MyProject.c,210 :: 		step_code[0] = 1;
	MOV	#lo_addr(_step_code), W1
	MOV.B	#1, W0
	MOV.B	W0, [W1]
;MyProject.c,211 :: 		step_code[1] = 1;
	MOV	#lo_addr(_step_code+1), W1
	MOV.B	#1, W0
	MOV.B	W0, [W1]
;MyProject.c,212 :: 		step_code[2] = 0;
	MOV	#lo_addr(_step_code+2), W1
	CLR	W0
	MOV.B	W0, [W1]
;MyProject.c,213 :: 		rotate(5916, step_code, 1); // 104 stepeni
	MOV	#1, W12
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

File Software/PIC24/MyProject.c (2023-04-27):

const int lookup[8][4] = {{1, 0, 0, 0}, {1, 1, 0, 0}, {0, 1, 0, 0}, {0, 1, 1, 0}, {0, 0, 1, 0}, {0, 0, 1, 1}, {0, 0, 0, 1}, {1, 0, 0, 1}};
signed char indexes[8] = {0, 0, 0, 0, 0, 0, 0, 0};
char uart_ch;
int flag = 0;
int m = 0;
int i = 0;
const int pauza = 1100;
char step_code[3] = {1, 1, 1};
int korak1 = 0;
char out[100] = "";

static inline void rotate(int step, char s[], int left_right){ // left_right = 1 - lijevo, left_right = -1 - desno
     i = 4*s[2] + 2*s[1] + s[0];
     LATB.F6 = s[2];
     LATB.F7 = s[1];
     LATB.F8 = s[0];
     while(step > 0){
         LATB.F13 = lookup[indexes[i]][0];
         LATB.F12 = lookup[indexes[i]][1];
         LATB.F11 = lookup[indexes[i]][2];
         LATB.F10 = lookup[indexes[i]][3];
         step--;
         indexes[i] += left_right;
         if (indexes[i] >= 8 && left_right == 1)
            indexes[i] = 0;
         if (indexes[i] < 0  && left_right == -1)
            indexes[i] = 7;
         Delay_us(pauza);
     }
     LATB.F13 = 0;
     LATB.F12 = 0;
     LATB.F11 = 0;
     LATB.F10 = 0;
     LATB.F6 = 1;
     LATB.F7 = 1;
     LATB.F8 = 1;
}

void uart_interrupt() iv IVT_ADDR_U1RXINTERRUPT ics ICS_AUTO {
  IFS0bits.U1RXIF = 0;
  uart_ch = UART1_Read();
  if(uart_ch == 'q'){
    m = 0;
    flag = 1;
  }
  else{
    out[m] = uart_ch;
    m++;
  }
}

void calibration(){
   LATB.F6 = 1;
   LATB.F7 = 0;
   LATB.F8 = 0;
   while(1){
      if(PORTB.F5 == 1)
         break;
      LATB.F13 = lookup[indexes[4]][0];
      LATB.F12 = lookup[indexes[4]][1];
      LATB.F11 = lookup[indexes[4]][2];
      LATB.F10 = lookup[indexes[4]][3];
      Delay_us(pauza);
      indexes[4]--;
      if (indexes[4] < 0)
        indexes[4] = 7;
   }
   LATB.F13 = 0;
   LATB.F12 = 0;
   LATB.F11 = 0;
   LATB.F10 = 0;
   step_code[0] = 0;
   step_code[1] = 0;
   step_code[2] = 1;
   rotate(910, step_code, 1);
   LATB.F6 = 0;
   LATB.F7 = 0;
   LATB.F8 = 1;
   while(1){
      if(PORTB.F15 == 1)
         break;
      LATB.F13 = lookup[indexes[1]][0];
      LATB.F12 = lookup[indexes[1]][1];
      LATB.F11 = lookup[indexes[1]][2];
      LATB.F10 = lookup[indexes[1]][3];
      Delay_us(pauza);
      indexes[1]--;
      if (indexes[1] < 0)
        indexes[1] = 7;
   }
   LATB.F13 = 0;
   LATB.F12 = 0;
   LATB.F11 = 0;
   LATB.F10 = 0;
   step_code[0] = 1;
   step_code[1] = 0;
   step_code[2] = 0;
   rotate(3000, step_code, 1);
}

void main() {
  OSCDIVbits.DIV = 0;
  
  ANSA = 0;
  ANSB = 0;

  TRISB = 0b0000010000000001;
  TRISA = 0b00000;
  
  ODCA = 0;
  ODCB = 0;
  
  LATA = 0;
  LATB = 0;

  Unlock_IOLOCK();
  PPS_Mapping_NoLock(3, _INPUT, _U1RX);
  PPS_Mapping_NoLock(2, _OUTPUT, _U1TX);
  Lock_IOLOCK();

  IEC0bits.U1RXIE = 1;
  IFS0bits.U1RXIF = 0;
  
  UART1_Init(9600);
  Delay_ms(100);
  calibration();
  LATB.F6 = 1;
  LATB.F7 = 1;
  LATB.F8 = 1;
  Delay_ms(100);
  while(1) {
     if(flag == 1){
        flag = 0;
        if(out[0] == 'A'){
           step_code[0] = 0;
           step_code[1] = 0;
           step_code[2] = 0;
           rotate(20, step_code, 1);
        }
        else if(out[0] == 'D'){
           step_code[0] = 0;
           step_code[1] = 0;
           step_code[2] = 0;
           rotate(20, step_code, -1);
        }
        else if(out[0] == 'J'){
           step_code[0] = 1;
           step_code[1] = 0;
           step_code[2] = 1;
           rotate(20, step_code, 1);
        }
        else if(out[0] == 'L'){
           step_code[0] = 1;
           step_code[1] = 0;
           step_code[2] = 1;
           rotate(20, step_code, -1);
        }
        else if(out[0] == 'O' && out[1] == 'L'){
           korak1 = atoi(out+2);
           step_code[0] = 0;
           step_code[1] = 1;
           step_code[2] = 0;
           rotate(korak1, step_code, 1);
           UART1_Write('1');
        }
        else if(out[0] == 'O' && out[1] == 'D'){
           korak1 = atoi(out+2);
           step_code[0] = 0;
           step_code[1] = 1;
           step_code[2] = 0;
           rotate(korak1, step_code, -1);
           UART1_Write('1');
        }
        else if(out[0] == 'K' && out[1] == 'A'){
           korak1 = atoi(out+2);
           step_code[0] = 1;
           step_code[1] = 0;
           step_code[2] = 0;
           rotate(korak1, step_code, -1);
        }
        else if(out[0] == 'N' && out[1] == '1'){
           step_code[0] = 1;
           step_code[1] = 1;
           step_code[2] = 0;
           rotate(2276, step_code, 1); // 40 stepeni
           UART1_Write('1');
        }
        else if(out[0] == 'N' && out[1] == '2'){
           step_code[0] = 1;
           step_code[1] = 1;
           step_code[2] = 0;
           rotate(2845, step_code, 1); // 50 stepeni
           UART1_Write('1');
        }
        else if(out[0] == 'N' && out[1] == '3'){
           step_code[0] = 1;
           step_code[1] = 1;
           step_code[2] = 0;
           rotate(3840, step_code, 1); // 67.5 stepeni
           UART1_Write('1');
        }
        else if(out[0] == 'N' && out[1] == '4'){
           step_code[0] = 1;
           step_code[1] = 1;
           step_code[2] = 0;
           rotate(4552, step_code, 1); // 80 stepeni
           UART1_Write('1');
        }
        else if(out[0] == 'N' && out[1] == '5'){
           step_code[0] = 1;
           step_code[1] = 1;
           step_code[2] = 0;
           rotate(5916, step_code, 1); // 104 stepeni
           UART1_Write('1');
        }
        else if(out[0] == 'I'){
           step_code[0] = 0;
           step_code[1] = 0;
           step_code[2] = 1;
           rotate(2000, step_code, 1);
           rotate(2000, step_code, -1);
        }
        else if(out[0] == 'C'){
           calibration();
        }
        else if(out[0] == 'B'){
           step_code[0] = 1;
           step_code[1] = 0;
           step_code[2] = 0;
           rotate(285, step_code, -1);
        }
        memset(out, 0, sizeof(out));
     }
  }
}

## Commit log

2022-12-30 Uradjena sema
    [schematic.kicad_pcb, schematic.kicad_sch]
2023-01-11 Rutiran PCB Prepravljena šema u skladu sa zahtjevima
    [ABLS-8_000MHZ-B2-T_ABR.step, CAP_0805J_AVX.step, D0016A.stp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]
2023-01-11 BOM fajl
    [BOM.csv]
2023-01-18 Dodat peti prekidac i u folderu Datasheet komponenti dodat datasheet koristenog multipleksera
    [schematic.kicad_sch]
2023-01-18 Dodat bajpas kondezator na ulaze za napajanje multipleksera
    [schematic.kicad_sch]
2023-01-25 Finalna verzija layout-a
    [DYY0016A.stp, NDE0003B.stp, schematic.kicad_pcb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]
2023-01-25 Napisane labele na ploci
    [schematic.kicad_pcb]
2023-01-25 Male izmjene oko labela
    [schematic.kicad_pcb]
2023-01-30 Izmjene na layout-u
    [schematic.csv, schematic.kicad_pcb, schematic.kicad_sch]
2023-01-30 Dodavanje labela
    [schematic.kicad_pcb]
2023-01-31 Final version
    [schematic-B_Cu.gbr, schematic-B_Mask.gbr, schematic-B_Paste.gbr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]
2023-01-31 Azuriran BOM fajl sa siframa i linkovima sa Mouser-a
    [BOM.csv]
2023-02-08 Izmjene u BOM fajlu
    [BOM.xlsx]
2023-02-08 Prethodna verzija BOM je obrisana
    [BOM.csv]
2023-04-08 Dodate su pocetne verzije kodova (software-a) za upravljanjem katapultom
    [MyProject.cfg]
2023-04-27 Revert "Software"
    [ABLS-8_000MHZ-B2-T_ABR.step, BOM.xlsx, CAP_0805J_AVX.step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]
2023-04-27 Ispravljena mala greska
    [MyProject.cfg]

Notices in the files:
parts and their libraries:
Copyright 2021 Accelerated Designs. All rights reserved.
